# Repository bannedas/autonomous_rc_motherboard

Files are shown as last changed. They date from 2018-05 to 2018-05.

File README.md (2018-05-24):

# Autonomous RC motherboard

Remake of Benjamin Vedder made project https://github.com/vedderb/rise_sdvp

## Main

```
- Raspberry Compute module 3
	- HDMI
	- CAM0
	- ETHERNET
	- USB HOST (4 USB OUT)
	- microSD
- DAS board
- 2.4GHz radio by CC2520 
	- CC2592 extender
	- External antenna
- 420MHz - 470MHz radio by CC120
	- External antenna
-RTK-GNSS
	- UBLOX NEO M8P module
	- External antenna

- 40V to 12V 3A power
- 12V to 5V 1A power
- 12V to 3V3 2A power
- 3V3 to 1V8 500mA power

- 2x CAN output
- 4x PWM output
- 1 uart output

- Status LED for everything

```

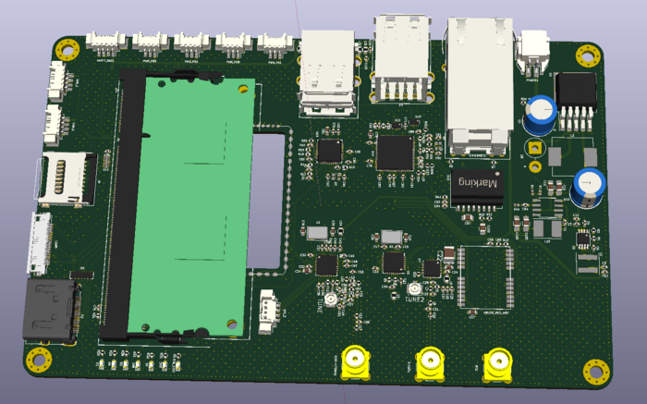
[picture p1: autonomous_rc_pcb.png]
PCB


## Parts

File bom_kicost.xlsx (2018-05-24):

Prj: | bom_kicost.xml |  |  |  | Board Qty: | 100
Co.: |  |  |  |  | Unit Cost: | $0.00
Prj date: | Thu 24 May 2018 02:57:31 PM CEST |  |  |  | Total Cost: | $0.00 |  |  |  | $0.00 | 0 |  |  |  | $0.00 | 0 |  |  |  | $0.00 | 0 |  |  |  | $0.00 | 0 |  |  |  | $0.00 | 0 |  |  |  | $0.00 | 0
$ date: | 2018-05-24 14:59:21
Global Part Info |  |  |  |  |  |  | Digi-Key |  |  |  |  | Farnell |  |  |  |  | Mouser |  |  |  |  | Newark |  |  |  |  | Rs Components |  |  |  |  | Tme
Refs | Value | Footprint | Manf# | Qty | Unit$ | Ext$ | Avail | Purch | Unit$ | Ext$ | Cat# | Avail | Purch | Unit$ | Ext$ | Cat# | Avail | Purch | Unit$ | Ext$ | Cat# | Avail | Purch | Unit$ | Ext$ | Cat# | Avail | Purch | Unit$ | Ext$ | Cat# | Avail | Purch | Unit$ | Ext$ | Cat#
A1 | RaspberryPiComputeModule | Don-Con:DDR2_TE_1473149-4 |  | 0 | $0.00 | $0.00
C1 | 10nF | Capacitors_SMD:C_0402 |  | 0 | $0.00 | $0.00
C10,C12 | 10uF | Capacitors_SMD:C_0805_HandSoldering |  | 0 | $0.00 | $0.00
C102 | 1n | Capacitors_SMD:C_0805 |  | 0 | $0.00 | $0.00
C105,C106 | 22uF | Capacitors_SMD:C_0805_HandSoldering |  | 0 | $0.00 | $0.00
C14 | 3.3nF | Capacitors_SMD:C_0402 |  | 0 | $0.00 | $0.00
C16,C19 | 15pF | Capacitors_SMD:C_0603 |  | 0 | $0.00 | $0.00
C2,C9,C11,C13 | 10uF | Capacitors_SMD:C_0402 |  | 0 | $0.00 | $0.00
C20,C23,C26 | 2.2uF | Capacitors_SMD:C_0402 |  | 0 | $0.00 | $0.00
C22 | 12uF | Capacitors_SMD:C_0402 |  | 0 | $0.00 | $0.00
C24,C25 | 1nF | Capacitors_SMD:C_0402 |  | 0 | $0.00 | $0.00
C27 | 12pF | Capacitors_SMD:C_0402 |  | 0 | $0.00 | $0.00
C28,C29,C53 | 2.2pF | Capacitors_SMD:C_0402 |  | 0 | $0.00 | $0.00
C3,C8 | 4.7uF | Capacitors_SMD:C_0402 |  | 0 | $0.00 | $0.00
C30 | 18pF | Capacitors_SMD:C_0402 |  | 0 | $0.00 | $0.00
C31 | 0.2pF | Capacitors_SMD:C_0402 |  | 0 | $0.00 | $0.00
C34,C57 | 2.2uF | Capacitors_SMD:C_0603 |  | 0 | $0.00 | $0.00
C35,C36 | 15p | Capacitors_SMD:C_0603 |  | 0 | $0.00 | $0.00
C4 | 1uF | Capacitors_SMD:C_0402 |  | 0 | $0.00 | $0.00
C45 | 1.8nF | Capacitors_SMD:C_0402 |  | 0 | $0.00 | $0.00
C48 | 39pF | Capacitors_SMD:C_0402 |  | 0 | $0.00 | $0.00
C5 | 100uF | Capacitor_THT:CP_Radial_D8.0mm_P3.50mm |  | 0 | $0.00 | $0.00
C50 | 56pF | Capacitors_SMD:C_0402 |  | 0 | $0.00 | $0.00
C52,C54,C55 | 5.1pF | Capacitors_SMD:C_0402 |  | 0 | $0.00 | $0.00
C56 | 6.2pF | Capacitors_SMD:C_0402 |  | 0 | $0.00 | $0.00
C6,C15,C17,C18,C21,C32,C33,C37-C44,C46,C47,C49,C51,C58 | 100nF | Capacitors_SMD:C_0402 |  | 0 | $0.00 | $0.00
C64,C67 | 9p | Capacitors_SMD:C_0402 | GRM1555C1H9R0CA01D | 0 | $0.00 | $0.00 | NonStk |  | $0.00 | $0.00 | 490-8232-1-ND (http://www.digikey.com/product-detail/en/murata-electronics-north-america/GRM1555C1H9R0CA01D/490-8232-1-ND/4380526) |  |  |  |  |  | NonStk |  | $0.00 | $0.00 | 81-GRM1555C1H9R0CA1D (https://www.mouser.com/ProductDetail/Murata-Electronics/GRM1555C1H9R0CA01D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)
C68 | 4u7 10V | Capacitors_SMD:C_0603 |  | 0 | $0.00 | $0.00
C7 | 1000uF | Capacitor_THT:CP_Radial_D8.0mm_P5.00mm | EEUFR1C102LB | 0 | $0.00 | $0.00 | 860 |  | $0.00 | $0.00 | P15332CT-ND (http://www.digikey.com/product-detail/en/panasonic-electronic-components/EEU-FR1C102LB/P15332CT-ND/3072212) |  |  |  |  |  | NonStk |  | $0.00 | $0.00 | 667-EEU-FR1C102LB (https://www.mouser.com/Search/Refine.aspx?Keyword=EEUFR1C102LB+) | 263 |  | $0.00 | $0.00 | 49W7393 (http://www.newark.com/webapp/wcs/stores/servlet/Search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) | 3800 |  |  |  | 708-3642 (http://it.rs-online.com/web/p/condensatori-elettrolitici/7083642P/)
C73 | 4u7 | Capacitors_SMD:C_0603 |  | 0 | $0.00 | $0.00
C74 | 1u | Capacitors_SMD:C_0402 |  | 0 | $0.00 | $0.00
C91,C92 | 6p | Capacitors_SMD:C_0402 |  | 0 | $0.00 | $0.00
C97 | 22n | Capacitors_SMD:C_0805 |  | 0 | $0.00 | $0.00
C98,C99,C103,C104 | 1n | Capacitors_SMD:C_0402 |  | 0 | $0.00 | $0.00
C59-C63,C65,C66,C69-C72,C76-C90,C93-C96,C100,C101 | 100n | Capacitors_SMD:C_0402 |  | 0 | $0.00 | $0.00
CAM0 | Conn_01x22 | MM-CONN:54548-2271 | 54548-2271 | 0 | $0.00 | $0.00 | 5312 |  | $0.00 | $0.00 | WM8828CT-ND (http://www.digikey.com/product-detail/en/molex-llc/0545482271/WM8828CT-ND/3197258) |  |  |  |  |  | 2773 |  | $0.00 | $0.00 | 538-54548-2271 (https://www.mouser.com/Search/Refine.aspx?Keyword=54548-2271+) | 24750 |  | $0.00 | $0.00 | 28W0905 (http://www.newark.com/molex/54548-2271/ffc-fpc-board-connector-zif-surface/dp/28W0905?st=54548-2271%20)
CAN_1,CAN_2,UART7_DAS1 | CONN_01X04 | Connectors_Molex:Molex_PicoBlade_53261-0471_04x1.25mm_Angled |  | 0 | $0.00 | $0.00
D1 | RTK_STAT | LEDs:LED_0603 |  | 0 | $0.00 | $0.00
D5,D6 | 3V3 | LEDs:LED_0603 |  | 0 | $0.00 | $0.00
D7 | 5V | LEDs:LED_0603 |  | 0 | $0.00 | $0.00
D8 | 1N5822 | PAUL-DIODE-SMD:D_DO-201AD_P5.08mm_Vertical_AnodeUp |  | 0 | $0.00 | $0.00
D2-D4 | LED | LEDs:LED_0603 |  | 0 | $0.00 | $0.00
ETHERNET1 | 08261L1T57-F | FS-Conn:0826-1L1T-57-F | 08261L1T57-F | 0 | $0.00 | $0.00 | 1929 |  | $0.00 | $0.00 | 507-1431-ND (http://www.digikey.com/scripts/DkSearch/dksus.dll?WT.z_header=search_go&lang=en) |  |  |  |  |  | 757 |  | $0.00 | $0.00 | 530-0826-1L1T-57-F (https://www.mouser.com/Search/Refine.aspx?Keyword=08261L1T57-F+)
J9 | Micro_SD_Card | Don-Con:microSD_Card_Receptacle_Wurth_693072010801 |  | 0 | $0.00 | $0.00
L1 | 4.7uH | Resistors_SMD:R_0805_HandSoldering | CPI0805E4R7R-10 | 0 | $0.00 | $0.00 | NonStk |  | $0.00 | $0.00 | CPI0805E4R7R-10-ND (http://www.digikey.com/scripts/DkSearch/dksus.dll?WT.z_header=search_go&lang=en) |  |  |  |  |  | 11435 |  | $0.00 | $0.00 | 875-CPI0805E4R7R-10 (https://www.mouser.com/Search/Refine.aspx?Keyword=CPI0805E4R7R-10+) | 1114 |  | $0.00 | $0.00 | 39Y3900 (http://www.newark.com/webapp/wcs/stores/servlet/Search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)
L11,L15 | 15n | Resistors_SMD:R_0402 |  | 0 | $0.00 | $0.00
L12,L13 | 27n | Resistors_SMD:R_0402 |  | 0 | $0.00 | $0.00
L16 | 43n | Resistors_SMD:R_0402 |  | 0 | $0.00 | $0.00
L17 | 22n | Resistors_SMD:R_0402 |  | 0 | $0.00 | $0.00
L18 | 56N | Resistors_SMD:R_0402 |  | 0 | $0.00 | $0.00
L19,L20 | BLM15PD121SN1D | Resistors_SMD:R_0402 |  | 0 | $0.00 | $0.00
L2 | 22uH | Inductors_SMD:L_Coilcraft_XAL5030 | VLCF5020T-220MR75-1 | 0 | $0.00 | $0.00 | 21355 |  | $0.00 | $0.00 | 445-3211-1-ND (http://www.digikey.com/product-detail/en/tdk-corporation/VLCF5020T-220MR75-1/445-3211-1-ND/1132852) |  |  |  |  |  | 6990 |  | $0.00 | $0.00 | 810-VLCF52T220MR751 (https://www.mouser.com/Search/Refine.aspx?Keyword=VLCF5020T-220MR75-1+) | NonStk |  | $0.00 | $0.00 | 91Y7126 (http://www.newark.com/tdk/vlcf5020t-220mr75-1/inductor-shielded-22uh-1a-20/dp/91Y7126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) | 280 |  | $0.00 | $0.00 | 614-2863 (http://it.rs-online.com/web/c/?searchTerm=VLCF5020T-220MR75-1+)
L29 | 4.7uH | Inductors_SMD:L_Taiyo-Yuden_NR-50xx_HandSoldering | SRN4018-4R7M | 0 | $0.00 | $0.00 | 38373 |  | $0.00 | $0.00 | SRN4018-4R7MCT-ND (http://www.digikey.com/product-detail/en/bourns-inc/SRN4018-4R7M/SRN4018-4R7MCT-ND/3821520) |  |  |  |  |  | 14094 |  | $0.00 | $0.00 | 652-SRN4018-4R7M (https://www.mouser.com/Search/Refine.aspx?Keyword=SRN4018-4R7M+) | 4833 |  | $0.00 | $0.00 | 54W0064 (http://www.newark.com/bourns/srn4018-4r7m/inductor-semi-shielded-4-7uh-1/dp/54W0064) | NonStk |  | $0.00 | $0.00 | 172-8355 (http://it.rs-online.com/web/p/induttori-avvolti-smd/1728355/)
L3 | 100uH | Inductors_SMD:L_Vishay_IHLP-4040 | MSS1210-104KED | 0 | $0.00 | $0.00 |  |  |  |  |  |  |  |  |  |  | 1939 |  | $0.00 | $0.00 | 994-MSS1210-104KED (https://www.mouser.com/ProductDetail/Coilcraft/MSS1210-104KED)
L4,L6,L14 | BEAD | Resistors_SMD:R_0603 | BLM18HE152SN1 | 0 | $0.00 | $0.00 | 94313 |  | $0.00 | $0.00 | 490-5216-1-ND (http://www.digikey.com/product-detail/en/murata-electronics-north-america/BLM18HE152SN1D/490-5216-1-ND/1948392) |  |  |  |  |  | NonStk |  |  |  | Not Assigned (https://www.mouser.com/ProductDetail/Murata-Electronics/BLM18HE152SN1) | 23044 |  | $0.00 | $0.00 | 87X8574 (http://www.newark.com/webapp/wcs/stores/servlet/Search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) | NonStk |  | $0.00 | $0.00 | 167-4980 (http://it.rs-online.com/web/p/ferriti/1674980/) | 22000 |  | $0.00 | $0.00 | BLM18HE152SN1D (https://www.tme.eu/en/details/blm18he152sn1d/ferrite-beads/murata/)
L5 | 4.7n | Resistors_SMD:R_0402 |  | 0 | $0.00 | $0.00
L7 | 1n | Resistors_SMD:R_0402 |  | 0 | $0.00 | $0.00
L8 | 2n | Resistors_SMD:R_0402 |  | 0 | $0.00 | $0.00
L9,L10 | 56n | Resistors_SMD:R_0402 |  | 0 | $0.00 | $0.00
L21-L28 | BLM18EG221SN1D | Resistors_SMD:R_0603 | BLM18EG221SN1D | 0 | $0.00 | $0.00 | 126995 |  | $0.00 | $0.00 | 490-3992-1-ND (http://www.digikey.com/product-detail/en/murata-electronics-north-america/BLM18EG221SN1D/490-3992-1-ND/1016252) |  |  |  |  |  |  |  |  |  |  | 6911 |  | $0.00 | $0.00 | 73M9090 (http://www.newark.com/webapp/wcs/stores/servlet/Search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) | 1375 |  | $0.00 | $0.00 | 724-1328 (http://it.rs-online.com/web/p/ferriti/7241328/) | NonStk |  | $0.00 | $0.00 | BLM18EG221SN1D (https://www.tme.eu/en/details/blm18eg221sn1d/ferrite-beads/murata/)
P1,P7 | USB_A_Vertical | Don-Con:USB_A_Stacked |  | 0 | $0.00 | $0.00
P2 | HDMI_PAUL | FS-Conn:HDMI_A_47151-1051 |  | 0 | $0.00 | $0.00
P3-P5 | SMA_SMD | Connectors:SMA_THT_Jack_Straight |  | 0 | $0.00 | $0.00
POWER1 | CONN_01X02 | Don-Con:DuraClik2 |  | 0 | $0.00 | $0.00
PWM_PA1,PWM_PB0,PWM_PB1,PWM_PB9 | CONN_01X03 | Connectors_Molex:Molex_PicoBlade_53261-0371_03x1.25mm_Angled |  | 0 | $0.00 | $0.00
R1 | 52.3k | Resistors_SMD:R_0402 |  | 0 | $0.00 | $0.00
R10 | 3.9K | Resistors_SMD:R_0402 |  | 0 | $0.00 | $0.00
R12 | 18R | Resistors_SMD:R_0402 |  | 0 | $0.00 | $0.00
R13 | 4.7R | Resistors_SMD:R_0402 |  | 0 | $0.00 | $0.00
R14,R16-R19 | 100k | Resistors_SMD:R_0402 |  | 0 | $0.00 | $0.00
R15 | 12k0 | Resistors_SMD:R_0402 |  | 0 | $0.00 | $0.00
R2,R33 | 10k | Resistors_SMD:R_0402 |  | 0 | $0.00 | $0.00
R20,R28,R29 | R | Resistors_SMD:R_0402 |  | 0 | $0.00 | $0.00
R22,R40 | 1M | Resistors_SMD:R_0402 |  | 0 | $0.00 | $0.00
R23 | 100K | Resistors_SMD:R_0402 |  | 0 | $0.00 | $0.00
R24 | DNP | Resistors_SMD:R_0402 |  | 0 | $0.00 | $0.00
R26 | 1k | Resistors_SMD:R_0402 |  | 0 | $0.00 | $0.00
R3 | 26.1k | Resistor_SMD:R_0402_1005Metric |  | 0 | $0.00 | $0.00
R34 | 12k4 | Resistors_SMD:R_0402 |  | 0 | $0.00 | $0.00
R35 | 12k | Resistors_SMD:R_0402 |  | 0 | $0.00 | $0.00
R4,R44 | 10k | Resistor_SMD:R_0402_1005Metric |  | 0 | $0.00 | $0.00
R41 | 10R | Resistors_SMD:R_0402 |  | 0 | $0.00 | $0.00
R42,R43 | 75R | Resistors_SMD:R_0402 |  | 0 | $0.00 | $0.00
R5,R25,R27,R30-R32 | 1K | Resistors_SMD:R_0402 |  | 0 | $0.00 | $0.00
R6,R7 | 120R | Resistors_SMD:R_0402 |  | 0 | $0.00 | $0.00
R8 | 10K | Resistors_SMD:R_0402 |  | 0 | $0.00 | $0.00
R9,R11 | 56K | Resistors_SMD:R_0402 |  | 0 | $0.00 | $0.00
R36-R39 | 49R9 | Resistors_SMD:R_0402 |  | 0 | $0.00 | $0.00
SPI_3 | CONN_01X04 | Connectors_Molex:Molex_PicoBlade_53398-0471_04x1.25mm_Straight |  | 0 | $0.00 | $0.00
U1 | MCP1603L | TO_SOT_Packages_SMD:TSOT-23-5 | MCP1603LT-180I/OS | 0 | $0.00 | $0.00 | NonStk |  | $0.00 | $0.00 | MCP1603LT-180I/OS-ND (http://www.digikey.com/scripts/DkSearch/dksus.dll?WT.z_header=search_go&lang=en) |  |  |  |  |  | NonStk |  | $0.00 | $0.00 | 579-MCP1603LT-180IOS (https://www.mouser.com/ProductDetail/Microchip-Technology/MCP1603LT-180I-OS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)
U10,U12 | ECMF04-4HSM10 | Housings_DFN_QFN:UDFN-10_1.35x2.6mm_Pitch0.5mm | ECMF04-4HSM10 | 0 | $0.00 | $0.00 | NonStk |  | $0.00 | $0.00 | 497-14242-2-ND (http://www.digikey.com/product-detail/en/stmicroelectronics/ECMF04-4HSM10/497-14242-2-ND/4552280) |  |  |  |  |  | 2949 |  | $0.00 | $0.00 | 511-ECMF04-4HSM10 (https://www.mouser.com/Search/Refine.aspx?Keyword=ECMF04-4HSM10+) | 3157 |  | $0.00 | $0.00 | 41Y1736 (http://www.newark.com/webapp/wcs/stores/servlet/Search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)
U11 | CM1624 | Don-Housing-DFN:UDFN-16-1EP_3.3x1.35mm_Pitch0.4mm | CM1624-08DE | 0 | $0.00 | $0.00 | NonStk |  | $0.00 | $0.00 | CM1624-08DEOSCT-ND (http://www.digikey.com/product-detail/en/on-semiconductor/CM1624-08DE/CM1624-08DEOSCT-ND/2442761) |  |  |  |  |  | NonStk |  | $0.00 | $0.00 | 748-CM1624-08DE (https://www.mouser.com/Search/Refine.aspx?Keyword=CM1624-08DE+) | NonStk |  | $0.00 | $0.00 | 55T2137 (http://www.newark.com/on-semiconductor/cm1624-08de/diode-emi-filter-esd-8ch-16-udfn/dp/55T2137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) | 50 |  | $0.00 | $0.00 | 800-9960 (http://it.rs-online.com/web/p/diodi-tvs/8009960/)
U13 | USB2514Bi | Don-Housing-QFN:QFN36_5m5X5m5 | USB2514B/M2 | 0 | $0.00 | $0.00 | 1776 |  | $0.00 | $0.00 | USB2514B/M2-ND (http://www.digikey.com/scripts/DkSearch/dksus.dll?WT.z_header=search_go&lang=en) |  |  |  |  |  | 4249 |  | $0.00 | $0.00 | 579-USB2514B/M2 (https://www.mouser.com/Search/Refine.aspx?Keyword=USB2514B%2FM2+) | 1421 |  | $0.00 | $0.00 | 31AC2618 (http://www.newark.com/webapp/wcs/stores/servlet/Search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) |  |  |  |  |  | NonStk |  | $0.00 | $0.00 | USB2514B/M2 (https://www.tme.eu/en/details/usb2514b_m2/usb-integrated-circuits/microchip-technology/)
U14 | LAN9514/LAN9514i | Housings_DFN_QFN:QFN-64-1EP_9x9mm_Pitch0.5mm | LAN9514-JZX | 0 | $0.00 | $0.00 | 2244 |  | $0.00 | $0.00 | 638-1087-ND (http://www.digikey.com/product-detail/en/microchip-technology/LAN9514-JZX/638-1087-ND/2166039) |  |  |  |  |  | 3560 |  | $0.00 | $0.00 | 886-LAN9514-JZX (https://www.mouser.com/ProductDetail/Microchip-Technology/LAN9514-JZX) | 34 |  | $0.00 | $0.00 | 69W9525 (http://www.newark.com/microchip/lan9514-jzx/usb-hub-ethernet-controller-100mbps/dp/69W9525?st=LAN9514-JZX%20) | 780 |  | $0.00 | $0.00 | 889-5130 (http://it.rs-online.com/web/p/controller-ethernet/8895130/)
U15 | Wurth_Magnetics_749010012A | FS-Magnetics:Wurth_749010012A | 749010012A | 0 | $0.00 | $0.00 |  |  |  |  |  |  |  |  |  |  |  |  |  |  |  | 428 |  | $0.00 | $0.00 | 55X3963 (http://www.newark.com/webapp/wcs/stores/servlet/Search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) | NonStk |  | $0.00 | $0.00 | 135-3807 (http://it.rs-online.com/web/p/trasformatori-per-reti-lan-ethernet/1353807/)
U16 | AP3512E | Package_SO:PowerIntegrations_SO-8 |  | 0 | $0.00 | $0.00
U2 | MCP16311/2 | Housings_SSOP:MSOP-8-1EP_3x3mm_Pitch0.65mm |  | 0 | $0.00 | $0.00
U3 | LM2576S-12/NOPB | Package_TO_SOT_SMD:TO-263-5_TabPin3 | LM2576S-12/NOPB | 0 | $0.00 | $0.00 | 2130 |  | $0.00 | $0.00 | LM2576S-12/NOPB-ND (http://www.digikey.com/scripts/DkSearch/dksus.dll?WT.z_header=search_go&lang=en) |  |  |  |  |  | 1401 |  | $0.00 | $0.00 | 926-LM2576S-12/NOPB (https://www.mouser.com/ProductDetail/Texas-Instruments/LM2576S-12-NOPB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) | 537 |  | $0.00 | $0.00 | 41K3687 (http://www.newark.com/webapp/wcs/stores/servlet/Search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) | 39 |  |  |  | 533-3197 (http://it.rs-online.com/web/p/convertitori-buck/5333197/) | 951 |  | $0.00 | $0.00 | LM2576S-12 (https://www.tme.eu/en/details/lm2576s-12/voltage-regulators-dcdc-circuits/texas-instruments/lm2576s-12nopb/)
U4 | Autopilot_module | Don-Mechanical:Autopilot |  | 0 | $0.00 | $0.00
U5 | ESD-8040 | FS-Diode:ESD8040 |  | 0 | $0.00 | $0.00
U6 | CC2520 | Housings_DFN_QFN:QFN-28-1EP_5x5mm_Pitch0.5mm | CC2520RHDR | 0 | $0.00 | $0.00 | 4009 |  | $0.00 | $0.00 | 296-22996-1-ND (http://www.digikey.com/product-detail/en/texas-instruments/CC2520RHDT/296-22996-1-ND/1770315) |  |  |  |  |  |  |  |  |  |  | 2900 |  | $0.00 | $0.00 | 33AC4955 (http://www.newark.com/webapp/wcs/stores/servlet/Search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)
U7 | CC2592 | Housings_DFN_QFN:QFN-16-1EP_4x4mm_Pitch0.65mm | CC2592RGVR | 0 | $0.00 | $0.00 | 7426 |  | $0.00 | $0.00 | 296-37475-1-ND (http://www.digikey.com/product-detail/en/texas-instruments/CC2592RGVR/296-37475-1-ND/4764659) |  |  |  |  |  | 4532 |  | $0.00 | $0.00 | 595-CC2592RGVR (https://www.mouser.com/ProductDetail/Texas-Instruments/CC2592RGVR) | 2787 |  | $0.00 | $0.00 | 33AC4958 (http://www.newark.com/webapp/wcs/stores/servlet/Search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)
U8 | CC112X | Housings_DFN_QFN:QFN-32-1EP_5x5mm_Pitch0.5mm |  | 0 | $0.00 | $0.00
U9 | UBLOX_NEO_M8P | PAUL-MODULE:U-BLOX-NEO-M8P |  | 0 | $0.00 | $0.00
X1 | 32Mhz | Crystals:Crystal_SMD_5032-4pin_5.0x3.2mm |  | 0 | $0.00 | $0.00
X2 | 32MHZ | Crystals:Crystal_SMD_5032-4pin_5.0x3.2mm |  | 0 | $0.00 | $0.00
X3 | XRCGB24M000F2P00R0 | Don-Timing:XRCGB |  | 0 | $0.00 | $0.00
X4 | XRCGB25M000F2P00R0 | Don-Timing:XRCGB |  | 0 | $0.00 | $0.00
Distributors scraped by KiCost® v.0.1.43 |  |  |  |  |  |  |  | 0 |  |  |  |  | 0 |  |  |  |  | 0 |  |  |  |  | 0 |  |  |  |  | 0 |  |  |  |  | 0
 |  |  |  |  |  |  |  | 0 | 0 | 0 |  |  | 0 | 0 | 0 |  |  | 0 | 0 | 0 |  |  | 0 | 0 | 0 |  |  | 0 | 0 | 0 |  |  | 0 | 0 | 0
 |  |  |  |  |  |  |  | 0 | 0 | 0 |  |  | 0 | 0 | 0 |  |  | 0 | 0 | 0 |  |  | 0 | 0 | 0 |  |  | 0 | 0 | 0 |  |  | 0 | 0 | 0
 |  |  |  |  |  |  |  | 0 | 0 | 0 |  |  | 0 | 0 | 0 |  |  | 0 | 0 | 0 |  |  | 0 | 0 | 0 |  |  | 0 | 0 | 0 |  |  | 0 | 0 | 0
 |  |  |  |  |  |  |  | 0 | 0 | 0 |  |  | 0 | 0 | 0 |  |  | 0 | 0 | 0 |  |  | 0 | 0 | 0 |  |  | 0 | 0 | 0 |  |  | 0 | 0 | 0
 |  |  |  |  |  |  |  | 0 | 0 | 0 |  |  | 0 | 0 | 0 |  |  | 0 | 0 | 0 |  |  | 0 | 0 | 0 |  |  | 0 | 0 | 0 |  |  | 0 | 0 | 0
 |  |  |  |  |  |  |  | 0 | 0 | 0 |  |  | 0 | 0 | 0 |  |  | 0 | 0 | 0 |  |  | 0 | 0 | 0 |  |  | 0 | 0 | 0 |  |  | 0 | 0 | 0
 |  |  |  |  |  |  |  | 0 | 0 | 0 |  |  | 0 | 0 | 0 |  |  | 0 | 0 | 0 |  |  | 0 | 0 | 0 |  |  | 0 | 0 | 0 |  |  | 0 | 0 | 0
 |  |  |  |  |  |  |  | 0 | 0 | 0 |  |  | 0 | 0 | 0 |  |  | 0 | 0 | 0 |  |  | 0 | 0 | 0 |  |  | 0 | 0 | 0 |  |  | 0 | 0 | 0
 |  |  |  |  |  |  |  | 0 | 0 | 0 |  |  | 0 | 0 | 0 |  |  | 0 | 0 | 0 |  |  | 0 | 0 | 0 |  |  | 0 | 0 | 0 |  |  | 0 | 0 | 0
 |  |  |  |  |  |  |  | 0 | 0 | 0 |  |  | 0 | 0 | 0 |  |  | 0 | 0 | 0 |  |  | 0 | 0 | 0 |  |  | 0 | 0 | 0 |  |  | 0 | 0 | 0
 |  |  |  |  |  |  |  | 0 | 0 | 0 |  |  | 0 | 0 | 0 |  |  | 0 | 0 | 0 |  |  | 0 | 0 | 0 |  |  | 0 | 0 | 0 |  |  | 0 | 0 | 0
 |  |  |  |  |  |  |  | 0 | 0 | 0 |  |  | 0 | 0 | 0 |  |  | 0 | 0 | 0 |  |  | 0 | 0 | 0 |  |  | 0 | 0 | 0 |  |  | 0 | 0 | 0
 |  |  |  |  |  |  |  | 0 | 0 | 0 |  |  | 0 | 0 | 0 |  |  | 0 | 0 | 0 |  |  | 0 | 0 | 0 |  |  | 0 | 0 | 0 |  |  | 0 | 0 | 0
 |  |  |  |  |  |  |  | 0 | 0 | 0 |  |  | 0 | 0 | 0 |  |  | 0 | 0 | 0 |  |  | 0 | 0 | 0 |  |  | 0 | 0 | 0 |  |  | 0 | 0 | 0
 |  |  |  |  |  |  |  | 0 | 0 | 0 |  |  | 0 | 0 | 0 |  |  | 0 | 0 | 0 |  |  | 0 | 0 | 0 |  |  | 0 | 0 | 0 |  |  | 0 | 0 | 0
 |  |  |  |  |  |  |  | 0 | 0 | 0 |  |  | 0 | 0 | 0 |  |  | 0 | 0 | 0 |  |  | 0 | 0 | 0 |  |  | 0 | 0 | 0 |  |  | 0 | 0 | 0
 |  |  |  |  |  |  |  | 0 | 0 | 0 |  |  | 0 | 0 | 0 |  |  | 0 | 0 | 0 |  |  | 0 | 0 | 0 |  |  | 0 | 0 | 0 |  |  | 0 | 0 | 0
 |  |  |  |  |  |  |  | 0 | 0 | 0 |  |  | 0 | 0 | 0 |  |  | 0 | 0 | 0 |  |  | 0 | 0 | 0 |  |  | 0 | 0 | 0 |  |  | 0 | 0 | 0
 |  |  |  |  |  |  |  | 0 | 0 | 0 |  |  | 0 | 0 | 0 |  |  | 0 | 0 | 0 |  |  | 0 | 0 | 0 |  |  | 0 | 0 | 0 |  |  | 0 | 0 | 0
 |  |  |  |  |  |  |  | 0 | 0 | 0 |  |  | 0 | 0 | 0 |  |  | 0 | 0 | 0 |  |  | 0 | 0 | 0 |  |  | 0 | 0 | 0 |  |  | 0 | 0 | 0
 |  |  |  |  |  |  |  | 0 | 0 | 0 |  |  | 0 | 0 | 0 |  |  | 0 | 0 | 0 |  |  | 0 | 0 | 0 |  |  | 0 | 0 | 0 |  |  | 0 | 0 | 0
 |  |  |  |  |  |  |  | 0 | 0 | 0 |  |  | 0 | 0 | 0 |  |  | 0 | 0 | 0 |  |  | 0 | 0 | 0 |  |  | 0 | 0 | 0 |  |  | 0 | 0 | 0
 |  |  |  |  |  |  |  | 0 | 0 | 0 |  |  | 0 | 0 | 0 |  |  | 0 | 0 | 0 |  |  | 0 | 0 | 0 |  |  | 0 | 0 | 0 |  |  | 0 | 0 | 0
 |  |  |  |  |  |  |  | 0 | 0 | 0 |  |  | 0 | 0 | 0 |  |  | 0 | 0 | 0 |  |  | 0 | 0 | 0 |  |  | 0 | 0 | 0 |  |  | 0 | 0 | 0
 |  |  |  |  |  |  |  | 0 | 0 | 0 |  |  | 0 | 0 | 0 |  |  | 0 | 0 | 0 |  |  | 0 | 0 | 0 |  |  | 0 | 0 | 0 |  |  | 0 | 0 | 0
 |  |  |  |  |  |  |  | 0 | 0 | 0 |  |  | 0 | 0 | 0 |  |  | 0 | 0 | 0 |  |  | 0 | 0 | 0 |  |  | 0 | 0 | 0 |  |  | 0 | 0 | 0
 |  |  |  |  |  |  |  | 0 | 0 | 0 |  |  | 0 | 0 | 0 |  |  | 0 | 0 | 0 |  |  | 0 | 0 | 0 |  |  | 0 | 0 | 0 |  |  | 0 | 0 | 0
 |  |  |  |  |  |  |  | 0 | 0 | 0 |  |  | 0 | 0 | 0 |  |  | 0 | 0 | 0 |  |  | 0 | 0 | 0 |  |  | 0 | 0 | 0 |  |  | 0 | 0 | 0
 |  |  |  |  |  |  |  | 0 | 0 | 0 |  |  | 0 | 0 | 0 |  |  | 0 | 0 | 0 |  |  | 0 | 0 | 0 |  |  | 0 | 0 | 0 |  |  | 0 | 0 | 0
 |  |  |  |  |  |  |  | 0 | 0 | 0 |  |  | 0 | 0 | 0 |  |  | 0 | 0 | 0 |  |  | 0 | 0 | 0 |  |  | 0 | 0 | 0 |  |  | 0 | 0 | 0
 |  |  |  |  |  |  |  | 0 | 0 | 0 |  |  | 0 | 0 | 0 |  |  | 0 | 0 | 0 |  |  | 0 | 0 | 0 |  |  | 0 | 0 | 0 |  |  | 0 | 0 | 0
 |  |  |  |  |  |  |  | 0 | 0 | 0 |  |  | 0 | 0 | 0 |  |  | 0 | 0 | 0 |  |  | 0 | 0 | 0 |  |  | 0 | 0 | 0 |  |  | 0 | 0 | 0
 |  |  |  |  |  |  |  | 0 | 0 | 0 |  |  | 0 | 0 | 0 |  |  | 0 | 0 | 0 |  |  | 0 | 0 | 0 |  |  | 0 | 0 | 0 |  |  | 0 | 0 | 0
 |  |  |  |  |  |  |  | 0 | 0 | 0 |  |  | 0 | 0 | 0 |  |  | 0 | 0 | 0 |  |  | 0 | 0 | 0 |  |  | 0 | 0 | 0 |  |  | 0 | 0 | 0
 |  |  |  |  |  |  |  | 0 | 0 | 0 |  |  | 0 | 0 | 0 |  |  | 0 | 0 | 0 |  |  | 0 | 0 | 0 |  |  | 0 | 0 | 0 |  |  | 0 | 0 | 0
 |  |  |  |  |  |  |  | 0 | 0 | 0 |  |  | 0 | 0 | 0 |  |  | 0 | 0 | 0 |  |  | 0 | 0 | 0 |  |  | 0 | 0 | 0 |  |  | 0 | 0 | 0
 |  |  |  |  |  |  |  | 0 | 0 | 0 |  |  | 0 | 0 | 0 |  |  | 0 | 0 | 0 |  |  | 0 | 0 | 0 |  |  | 0 | 0 | 0 |  |  | 0 | 0 | 0
 |  |  |  |  |  |  |  | 0 | 0 | 0 |  |  | 0 | 0 | 0 |  |  | 0 | 0 | 0 |  |  | 0 | 0 | 0 |  |  | 0 | 0 | 0 |  |  | 0 | 0 | 0
 |  |  |  |  |  |  |  | 0 | 0 | 0 |  |  | 0 | 0 | 0 |  |  | 0 | 0 | 0 |  |  | 0 | 0 | 0 |  |  | 0 | 0 | 0 |  |  | 0 | 0 | 0
 |  |  |  |  |  |  |  | 0 | 0 | 0 |  |  | 0 | 0 | 0 |  |  | 0 | 0 | 0 |  |  | 0 | 0 | 0 |  |  | 0 | 0 | 0 |  |  | 0 | 0 | 0
 |  |  |  |  |  |  |  | 0 | 0 | 0 |  |  | 0 | 0 | 0 |  |  | 0 | 0 | 0 |  |  | 0 | 0 | 0 |  |  | 0 | 0 | 0 |  |  | 0 | 0 | 0
 |  |  |  |  |  |  |  | 0 | 0 | 0 |  |  | 0 | 0 | 0 |  |  | 0 | 0 | 0 |  |  | 0 | 0 | 0 |  |  | 0 | 0 | 0 |  |  | 0 | 0 | 0
 |  |  |  |  |  |  |  | 0 | 0 | 0 |  |  | 0 | 0 | 0 |  |  | 0 | 0 | 0 |  |  | 0 | 0 | 0 |  |  | 0 | 0 | 0 |  |  | 0 | 0 | 0
 |  |  |  |  |  |  |  | 0 | 0 | 0 |  |  | 0 | 0 | 0 |  |  | 0 | 0 | 0 |  |  | 0 | 0 | 0 |  |  | 0 | 0 | 0 |  |  | 0 | 0 | 0
 |  |  |  |  |  |  |  | 0 | 0 | 0 |  |  | 0 | 0 | 0 |  |  | 0 | 0 | 0 |  |  | 0 | 0 | 0 |  |  | 0 | 0 | 0 |  |  | 0 | 0 | 0
 |  |  |  |  |  |  |  | 0 | 0 | 0 |  |  | 0 | 0 | 0 |  |  | 0 | 0 | 0 |  |  | 0 | 0 | 0 |  |  | 0 | 0 | 0 |  |  | 0 | 0 | 0
 |  |  |  |  |  |  |  | 0 | 0 | 0 |  |  | 0 | 0 | 0 |  |  | 0 | 0 | 0 |  |  | 0 | 0 | 0 |  |  | 0 | 0 | 0 |  |  | 0 | 0 | 0
 |  |  |  |  |  |  |  | 0 | 0 | 0 |  |  | 0 | 0 | 0 |  |  | 0 | 0 | 0 |  |  | 0 | 0 | 0 |  |  | 0 | 0 | 0 |  |  | 0 | 0 | 0
 |  |  |  |  |  |  |  | 0 | 0 | 0 |  |  | 0 | 0 | 0 |  |  | 0 | 0 | 0 |  |  | 0 | 0 | 0 |  |  | 0 | 0 | 0 |  |  | 0 | 0 | 0
 |  |  |  |  |  |  |  | 0 | 0 | 0 |  |  | 0 | 0 | 0 |  |  | 0 | 0 | 0 |  |  | 0 | 0 | 0 |  |  | 0 | 0 | 0 |  |  | 0 | 0 | 0
 |  |  |  |  |  |  |  | 0 | 0 | 0 |  |  | 0 | 0 | 0 |  |  | 0 | 0 | 0 |  |  | 0 | 0 | 0 |  |  | 0 | 0 | 0 |  |  | 0 | 0 | 0
 |  |  |  |  |  |  |  | 0 | 0 | 0 |  |  | 0 | 0 | 0 |  |  | 0 | 0 | 0 |  |  | 0 | 0 | 0 |  |  | 0 | 0 | 0 |  |  | 0 | 0 | 0
 |  |  |  |  |  |  |  | 0 | 0 | 0 |  |  | 0 | 0 | 0 |  |  | 0 | 0 | 0 |  |  | 0 | 0 | 0 |  |  | 0 | 0 | 0 |  |  | 0 | 0 | 0
 |  |  |  |  |  |  |  | 0 | 0 | 0 |  |  | 0 | 0 | 0 |  |  | 0 | 0 | 0 |  |  | 0 | 0 | 0 |  |  | 0 | 0 | 0 |  |  | 0 | 0 | 0
 |  |  |  |  |  |  |  | 0 | 0 | 0 |  |  | 0 | 0 | 0 |  |  | 0 | 0 | 0 |  |  | 0 | 0 | 0 |  |  | 0 | 0 | 0 |  |  | 0 | 0 | 0
 |  |  |  |  |  |  |  | 0 | 0 | 0 |  |  | 0 | 0 | 0 |  |  | 0 | 0 | 0 |  |  | 0 | 0 | 0 |  |  | 0 | 0 | 0 |  |  | 0 | 0 | 0
 |  |  |  |  |  |  |  | 0 | 0 | 0 |  |  | 0 | 0 | 0 |  |  | 0 | 0 | 0 |  |  | 0 | 0 | 0 |  |  | 0 | 0 | 0 |  |  | 0 | 0 | 0
 |  |  |  |  |  |  |  | 0 | 0 | 0 |  |  | 0 | 0 | 0 |  |  | 0 | 0 | 0 |  |  | 0 | 0 | 0 |  |  | 0 | 0 | 0 |  |  | 0 | 0 | 0
 |  |  |  |  |  |  |  | 0 | 0 | 0 |  |  | 0 | 0 | 0 |  |  | 0 | 0 | 0 |  |  | 0 | 0 | 0 |  |  | 0 | 0 | 0 |  |  | 0 | 0 | 0
 |  |  |  |  |  |  |  | 0 | 0 | 0 |  |  | 0 | 0 | 0 |  |  | 0 | 0 | 0 |  |  | 0 | 0 | 0 |  |  | 0 | 0 | 0 |  |  | 0 | 0 | 0
 |  |  |  |  |  |  |  | 0 | 0 | 0 |  |  | 0 | 0 | 0 |  |  | 0 | 0 | 0 |  |  | 0 | 0 | 0 |  |  | 0 | 0 | 0 |  |  | 0 | 0 | 0
 |  |  |  |  |  |  |  | 0 | 0 | 0 |  |  | 0 | 0 | 0 |  |  | 0 | 0 | 0 |  |  | 0 | 0 | 0 |  |  | 0 | 0 | 0 |  |  | 0 | 0 | 0
 |  |  |  |  |  |  |  | 0 | 0 | 0 |  |  | 0 | 0 | 0 |  |  | 0 | 0 | 0 |  |  | 0 | 0 | 0 |  |  | 0 | 0 | 0 |  |  | 0 | 0 | 0
 |  |  |  |  |  |  |  | 0 | 0 | 0 |  |  | 0 | 0 | 0 |  |  | 0 | 0 | 0 |  |  | 0 | 0 | 0 |  |  | 0 | 0 | 0 |  |  | 0 | 0 | 0
 |  |  |  |  |  |  |  | 0 | 0 | 0 |  |  | 0 | 0 | 0 |  |  | 0 | 0 | 0 |  |  | 0 | 0 | 0 |  |  | 0 | 0 | 0 |  |  | 0 | 0 | 0
 |  |  |  |  |  |  |  | 0 | 0 | 0 |  |  | 0 | 0 | 0 |  |  | 0 | 0 | 0 |  |  | 0 | 0 | 0 |  |  | 0 | 0 | 0 |  |  | 0 | 0 | 0
 |  |  |  |  |  |  |  | 0 | 0 | 0 |  |  | 0 | 0 | 0 |  |  | 0 | 0 | 0 |  |  | 0 | 0 | 0 |  |  | 0 | 0 | 0 |  |  | 0 | 0 | 0
 |  |  |  |  |  |  |  | 0 | 0 | 0 |  |  | 0 | 0 | 0 |  |  | 0 | 0 | 0 |  |  | 0 | 0 | 0 |  |  | 0 | 0 | 0 |  |  | 0 | 0 | 0
 |  |  |  |  |  |  |  | 0 | 0 | 0 |  |  | 0 | 0 | 0 |  |  | 0 | 0 | 0 |  |  | 0 | 0 | 0 |  |  | 0 | 0 | 0 |  |  | 0 | 0 | 0
 |  |  |  |  |  |  |  | 0 | 0 | 0 |  |  | 0 | 0 | 0 |  |  | 0 | 0 | 0 |  |  | 0 | 0 | 0 |  |  | 0 | 0 | 0 |  |  | 0 | 0 | 0
 |  |  |  |  |  |  |  | 0 | 0 | 0 |  |  | 0 | 0 | 0 |  |  | 0 | 0 | 0 |  |  | 0 | 0 | 0 |  |  | 0 | 0 | 0 |  |  | 0 | 0 | 0
 |  |  |  |  |  |  |  | 0 | 0 | 0 |  |  | 0 | 0 | 0 |  |  | 0 | 0 | 0 |  |  | 0 | 0 | 0 |  |  | 0 | 0 | 0 |  |  | 0 | 0 | 0
 |  |  |  |  |  |  |  | 0 | 0 | 0 |  |  | 0 | 0 | 0 |  |  | 0 | 0 | 0 |  |  | 0 | 0 | 0 |  |  | 0 | 0 | 0 |  |  | 0 | 0 | 0
 |  |  |  |  |  |  |  | 0 | 0 | 0 |  |  | 0 | 0 | 0 |  |  | 0 | 0 | 0 |  |  | 0 | 0 | 0 |  |  | 0 | 0 | 0 |  |  | 0 | 0 | 0
 |  |  |  |  |  |  |  | 0 | 0 | 0 |  |  | 0 | 0 | 0 |  |  | 0 | 0 | 0 |  |  | 0 | 0 | 0 |  |  | 0 | 0 | 0 |  |  | 0 | 0 | 0
 |  |  |  |  |  |  |  | 0 | 0 | 0 |  |  | 0 | 0 | 0 |  |  | 0 | 0 | 0 |  |  | 0 | 0 | 0 |  |  | 0 | 0 | 0 |  |  | 0 | 0 | 0
 |  |  |  |  |  |  |  | 0 | 0 | 0 |  |  | 0 | 0 | 0 |  |  | 0 | 0 | 0 |  |  | 0 | 0 | 0 |  |  | 0 | 0 | 0 |  |  | 0 | 0 | 0
 |  |  |  |  |  |  |  | 0 | 0 | 0 |  |  | 0 | 0 | 0 |  |  | 0 | 0 | 0 |  |  | 0 | 0 | 0 |  |  | 0 | 0 | 0 |  |  | 0 | 0 | 0
 |  |  |  |  |  |  |  | 0 | 0 | 0 |  |  | 0 | 0 | 0 |  |  | 0 | 0 | 0 |  |  | 0 | 0 | 0 |  |  | 0 | 0 | 0 |  |  | 0 | 0 | 0
 |  |  |  |  |  |  |  | 0 | 0 | 0 |  |  | 0 | 0 | 0 |  |  | 0 | 0 | 0 |  |  | 0 | 0 | 0 |  |  | 0 | 0 | 0 |  |  | 0 | 0 | 0
 |  |  |  |  |  |  |  | 0 | 0 | 0 |  |  | 0 | 0 | 0 |  |  | 0 | 0 | 0 |  |  | 0 | 0 | 0 |  |  | 0 | 0 | 0 |  |  | 0 | 0 | 0
 |  |  |  |  |  |  |  | 0 | 0 | 0 |  |  | 0 | 0 | 0 |  |  | 0 | 0 | 0 |  |  | 0 | 0 | 0 |  |  | 0 | 0 | 0 |  |  | 0 | 0 | 0
 |  |  |  |  |  |  |  | 0 | 0 | 0 |  |  | 0 | 0 | 0 |  |  | 0 | 0 | 0 |  |  | 0 | 0 | 0 |  |  | 0 | 0 | 0 |  |  | 0 | 0 | 0
 |  |  |  |  |  |  |  | 0 | 0 | 0 |  |  | 0 | 0 | 0 |  |  | 0 | 0 | 0 |  |  | 0 | 0 | 0 |  |  | 0 | 0 | 0 |  |  | 0 | 0 | 0
 |  |  |  |  |  |  |  | 0 | 0 | 0 |  |  | 0 | 0 | 0 |  |  | 0 | 0 | 0 |  |  | 0 | 0 | 0 |  |  | 0 | 0 | 0 |  |  | 0 | 0 | 0
 |  |  |  |  |  |  |  | 0 | 0 | 0 |  |  | 0 | 0 | 0 |  |  | 0 | 0 | 0 |  |  | 0 | 0 | 0 |  |  | 0 | 0 | 0 |  |  | 0 | 0 | 0
 |  |  |  |  |  |  |  | 0 | 0 | 0 |  |  | 0 | 0 | 0 |  |  | 0 | 0 | 0 |  |  | 0 | 0 | 0 |  |  | 0 | 0 | 0 |  |  | 0 | 0 | 0
 |  |  |  |  |  |  |  | 0 | 0 | 0 |  |  | 0 | 0 | 0 |  |  | 0 | 0 | 0 |  |  | 0 | 0 | 0 |  |  | 0 | 0 | 0 |  |  | 0 | 0 | 0
 |  |  |  |  |  |  |  | 0 | 0 | 0 |  |  | 0 | 0 | 0 |  |  | 0 | 0 | 0 |  |  | 0 | 0 | 0 |  |  | 0 | 0 | 0 |  |  | 0 | 0 | 0
 |  |  |  |  |  |  |  | 0 | 0 | 0 |  |  | 0 | 0 | 0 |  |  | 0 | 0 | 0 |  |  | 0 | 0 | 0 |  |  | 0 | 0 | 0 |  |  | 0 | 0 | 0
 |  |  |  |  |  |  |  | 0 | 0 | 0 |  |  | 0 | 0 | 0 |  |  | 0 | 0 | 0 |  |  | 0 | 0 | 0 |  |  | 0 | 0 | 0 |  |  | 0 | 0 | 0
 |  |  |  |  |  |  |  | 0 | 0 | 0 |  |  | 0 | 0 | 0 |  |  | 0 | 0 | 0 |  |  | 0 | 0 | 0 |  |  | 0 | 0 | 0 |  |  | 0 | 0 | 0
 |  |  |  |  |  |  |  | 0 | 0 | 0 |  |  | 0 | 0 | 0 |  |  | 0 | 0 | 0 |  |  | 0 | 0 | 0 |  |  | 0 | 0 | 0 |  |  | 0 | 0 | 0
 |  |  |  |  |  |  |  | 0 | 0 | 0 |  |  | 0 | 0 | 0 |  |  | 0 | 0 | 0 |  |  | 0 | 0 | 0 |  |  | 0 | 0 | 0 |  |  | 0 | 0 | 0
 |  |  |  |  |  |  |  | 0 | 0 | 0 |  |  | 0 | 0 | 0 |  |  | 0 | 0 | 0 |  |  | 0 | 0 | 0 |  |  | 0 | 0 | 0 |  |  | 0 | 0 | 0
 |  |  |  |  |  |  |  | 0 | 0 | 0 |  |  | 0 | 0 | 0 |  |  | 0 | 0 | 0 |  |  | 0 | 0 | 0 |  |  | 0 | 0 | 0 |  |  | 0 | 0 | 0
 |  |  |  |  |  |  |  | 0 | 0 | 0 |  |  | 0 | 0 | 0 |  |  | 0 | 0 | 0 |  |  | 0 | 0 | 0 |  |  | 0 | 0 | 0 |  |  | 0 | 0 | 0
 |  |  |  |  |  |  |  | 0 | 0 | 0 |  |  | 0 | 0 | 0 |  |  | 0 | 0 | 0 |  |  | 0 | 0 | 0 |  |  | 0 | 0 | 0 |  |  | 0 | 0 | 0
 |  |  |  |  |  |  |  | 0 | 0 | 0 |  |  | 0 | 0 | 0 |  |  | 0 | 0 | 0 |  |  | 0 | 0 | 0 |  |  | 0 | 0 | 0 |  |  | 0 | 0 | 0
 |  |  |  |  |  |  |  | 0 | 0 | 0 |  |  | 0 | 0 | 0 |  |  | 0 | 0 | 0 |  |  | 0 | 0 | 0 |  |  | 0 | 0 | 0 |  |  | 0 | 0 | 0
 |  |  |  |  |  |  |  | 0 | 0 | 0 |  |  | 0 | 0 | 0 |  |  | 0 | 0 | 0 |  |  | 0 | 0 | 0 |  |  | 0 | 0 | 0 |  |  | 0 | 0 | 0
 |  |  |  |  |  |  |  | 0 | 0 | 0 |  |  | 0 | 0 | 0 |  |  | 0 | 0 | 0 |  |  | 0 | 0 | 0 |  |  | 0 | 0 | 0 |  |  | 0 | 0 | 0
 |  |  |  |  |  |  |  | 0 | 0 | 0 |  |  | 0 | 0 | 0 |  |  | 0 | 0 | 0 |  |  | 0 | 0 | 0 |  |  | 0 | 0 | 0 |  |  | 0 | 0 | 0
 |  |  |  |  |  |  |  | 0 | 0 | 0 |  |  | 0 | 0 | 0 |  |  | 0 | 0 | 0 |  |  | 0 | 0 | 0 |  |  | 0 | 0 | 0 |  |  | 0 | 0 | 0
 |  |  |  |  |  |  |  | 0 | 0 | 0 |  |  | 0 | 0 | 0 |  |  | 0 | 0 | 0 |  |  | 0 | 0 | 0 |  |  | 0 | 0 | 0 |  |  | 0 | 0 | 0
 |  |  |  |  |  |  |  | 0 | 0 | 0 |  |  | 0 | 0 | 0 |  |  | 0 | 0 | 0 |  |  | 0 | 0 | 0 |  |  | 0 | 0 | 0 |  |  | 0 | 0 | 0
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

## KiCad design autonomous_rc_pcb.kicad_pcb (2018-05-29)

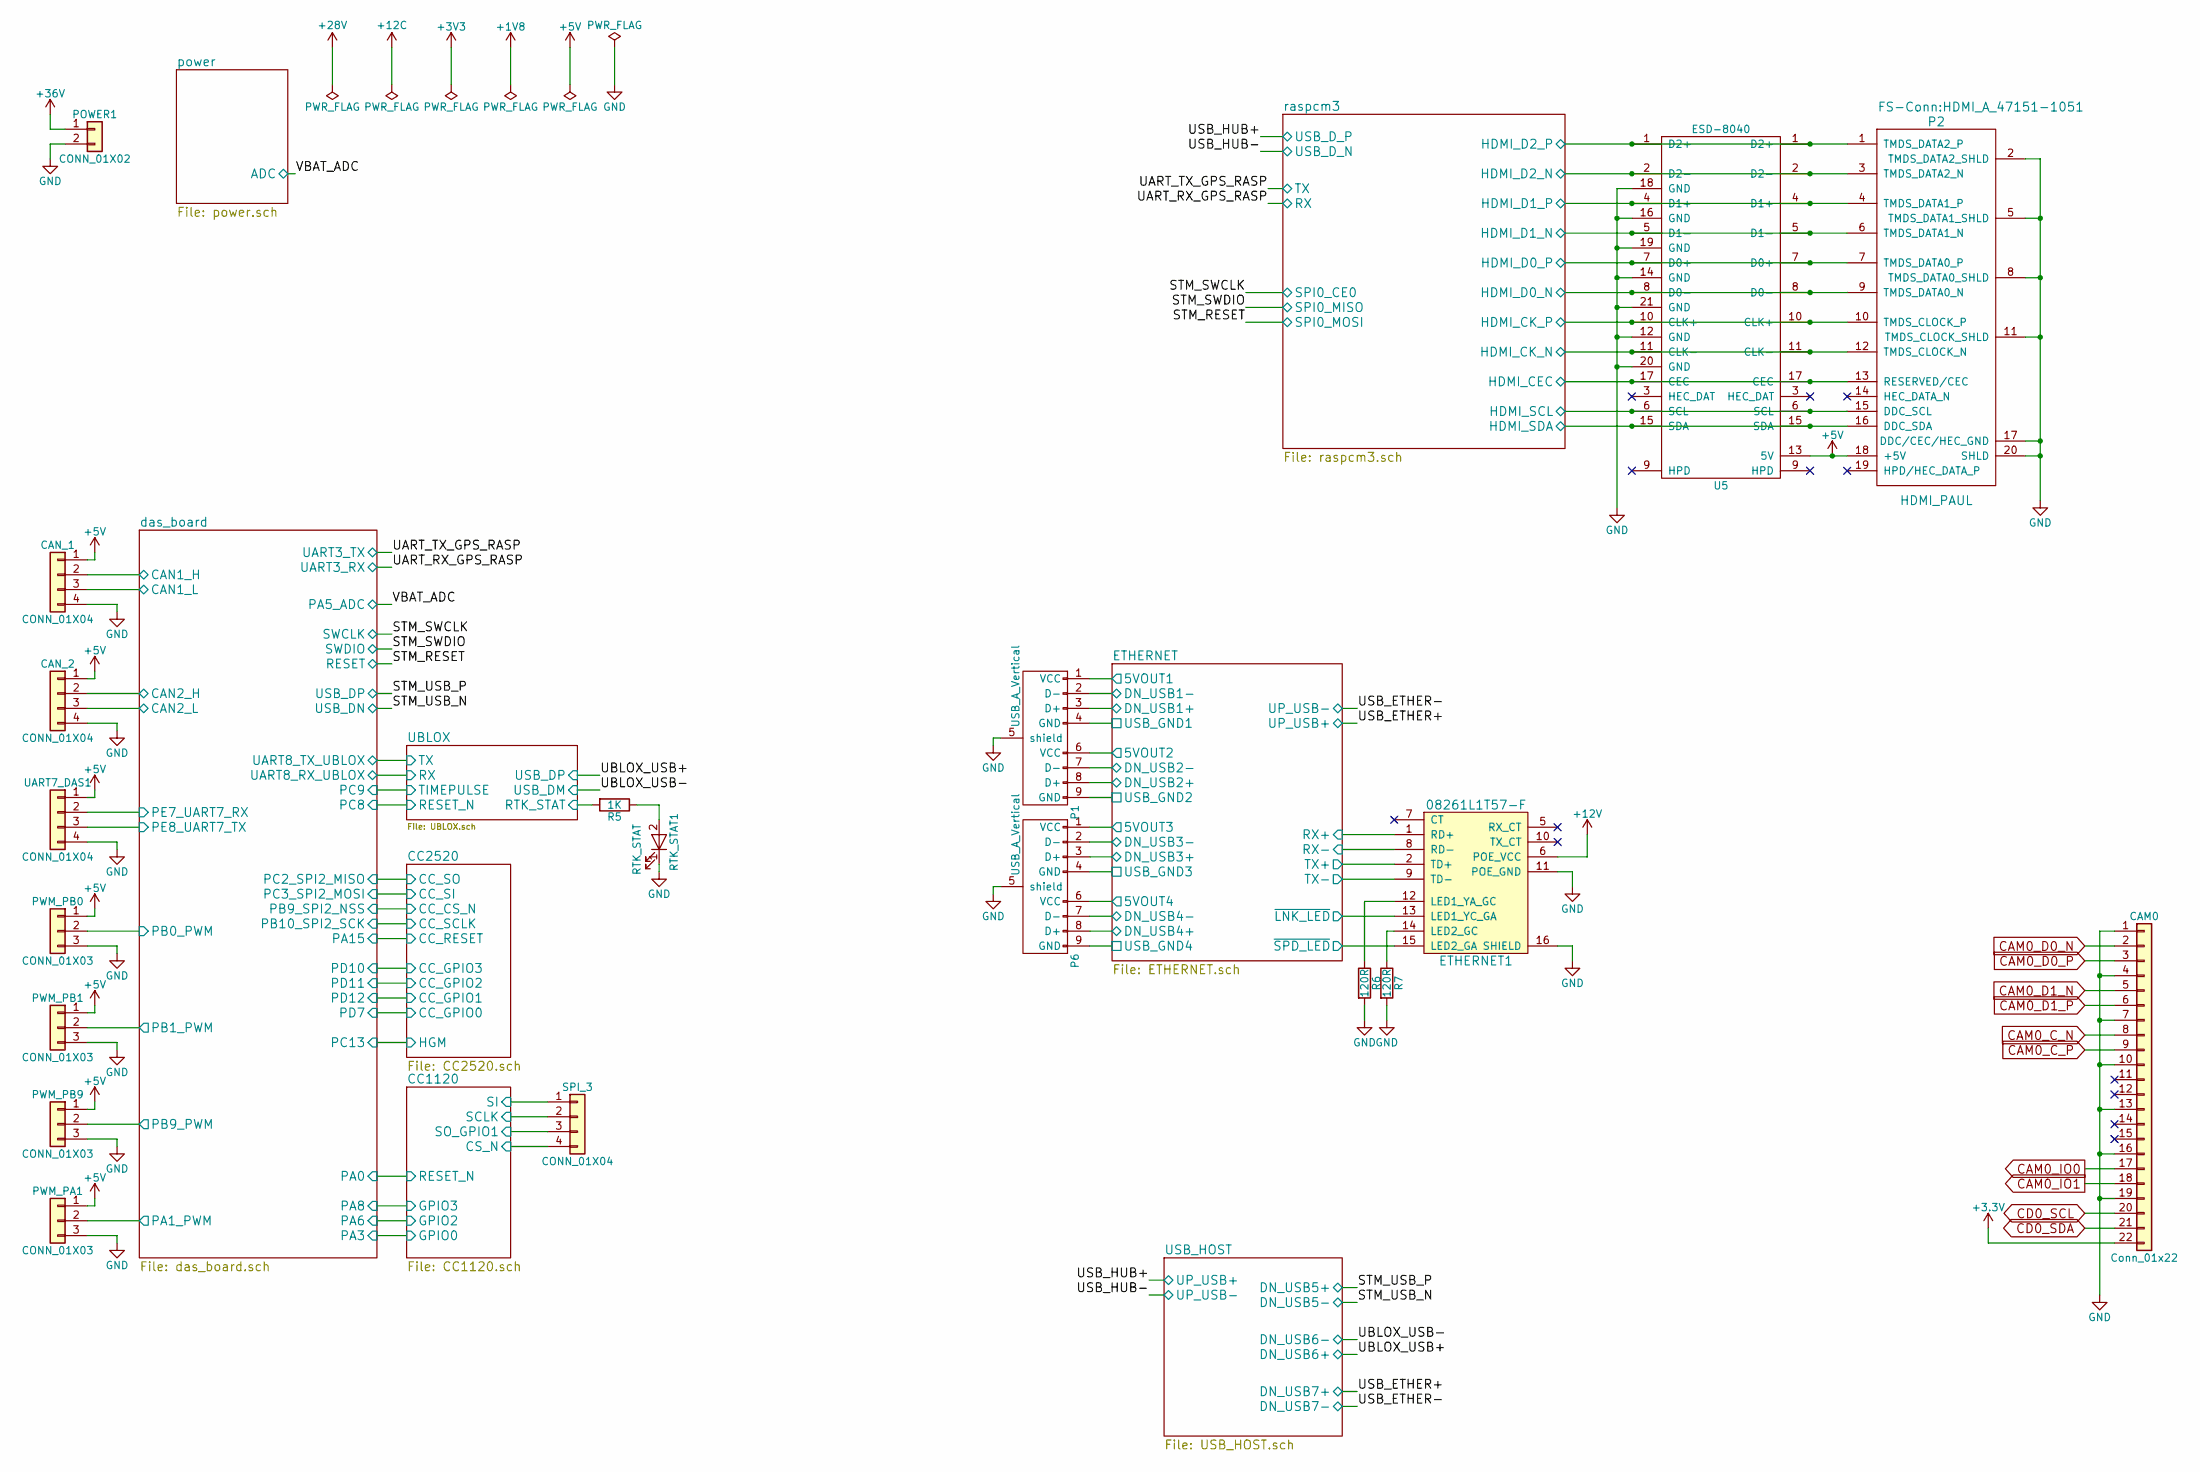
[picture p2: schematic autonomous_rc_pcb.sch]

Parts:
CAM0: Conn_01x22; 54548-2271; MPN 54548-2271
CAN_1, CAN_2: CONN_01X04; Molex_PicoBlade_53261-0471_04x1.25mm_Angled
ETHERNET1: 08261L1T57-F; 0826-1L1T-57-F; MPN 08261L1T57-F
P1, P6: USB_A_Vertical; USB-A-vertical
P2: HDMI_PAUL; HDMI_A_47151-1051
POWER1: CONN_01X02; DuraClik2
PWM_PA1: CONN_01X03; Molex_PicoBlade_53261-0371_03x1.25mm_Angled
PWM_PB0, PWM_PB1, PWM_PB9: CONN_01X03; Molex_PicoBlade_53261-0371_03x1.25mm_Angled
R5: 1K; R_0402
R6, R7: 120R; R_0402
RTK_STAT1: RTK_STAT; LED_0603
SPI_3: CONN_01X04; Molex_PicoBlade_53398-0471_04x1.25mm_Straight
U5: ESD-8040; ESD8040
UART7_DAS1: CONN_01X04; Molex_PicoBlade_53261-0471_04x1.25mm_Angled

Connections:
+5V: CAN_1.1, CAN_2.1, P2.18 (+5V), PWM_PA1.1, PWM_PB0.1, PWM_PB1.1, PWM_PB9.1, U5.13 (5V), UART7_DAS1.1; also elsewhere on the board
+12V: ETHERNET1.6 (POE_VCC); also elsewhere on the board
+36V: POWER1.1; also elsewhere on the board
/CC1120/CS_N: SPI_3.4; also elsewhere on the board
/CC1120/SCLK: SPI_3.2; also elsewhere on the board
/CC1120/SI: SPI_3.1; also elsewhere on the board
/CC1120/SO_GPIO1: SPI_3.3; also elsewhere on the board
/ETHERNET/5VOUT3: P1.1 (VCC); also elsewhere on the board
/ETHERNET/5VOUT4: P1.6 (VCC); also elsewhere on the board
/ETHERNET/DN_USB3+: P1.3 (D+); also elsewhere on the board
/ETHERNET/DN_USB3-: P1.2 (D-); also elsewhere on the board
/ETHERNET/DN_USB4+: P1.8 (D+); also elsewhere on the board
/ETHERNET/DN_USB4-: P1.7 (D-); also elsewhere on the board
/ETHERNET/RX+: ETHERNET1.1 (RD+); also elsewhere on the board
/ETHERNET/RX-: ETHERNET1.8 (RD-); also elsewhere on the board
/ETHERNET/TX+: ETHERNET1.2 (TD+); also elsewhere on the board
/ETHERNET/TX-: ETHERNET1.9 (TD-); also elsewhere on the board
/ETHERNET/USB_GND3: P1.4 (GND); also elsewhere on the board
/ETHERNET/USB_GND4: P1.9 (GND); also elsewhere on the board
/ETHERNET/~LNK_LED: ETHERNET1.13 (LED1_YC_GA); also elsewhere on the board
/ETHERNET/~SPD_LED: ETHERNET1.15 (LED2_GA); also elsewhere on the board
/UBLOX/RTK_STAT: R5.2; also elsewhere on the board
/das_board/CAN1_H: CAN_1.2; also elsewhere on the board
/das_board/CAN1_L: CAN_1.3; also elsewhere on the board
/das_board/CAN2_H: CAN_2.2; also elsewhere on the board
/das_board/CAN2_L: CAN_2.3; also elsewhere on the board
/das_board/PA1_PWM: PWM_PA1.2; also elsewhere on the board
/das_board/PB0_PWM: PWM_PB0.2; also elsewhere on the board
/das_board/PB1_PWM: PWM_PB1.2; also elsewhere on the board
/das_board/PB9_PWM: PWM_PB9.2; also elsewhere on the board
/das_board/PE7_UART7_RX: UART7_DAS1.2; also elsewhere on the board
/das_board/PE8_UART7_TX: UART7_DAS1.3; also elsewhere on the board
/raspcm3/HDMI_CEC: P2.13 (RESERVED/CEC), U5.17 (CEC); also elsewhere on the board
/raspcm3/HDMI_CK_N: P2.12 (TMDS_CLOCK_N), U5.11 (CLK-); also elsewhere on the board
/raspcm3/HDMI_CK_P: P2.10 (TMDS_CLOCK_P), U5.10 (CLK+); also elsewhere on the board
/raspcm3/HDMI_D0_N: P2.9 (TMDS_DATA0_N), U5.8 (D0-); also elsewhere on the board
/raspcm3/HDMI_D0_P: P2.7 (TMDS_DATA0_P), U5.7 (D0+); also elsewhere on the board
/raspcm3/HDMI_D1_N: P2.6 (TMDS_DATA1_N), U5.5 (D1-); also elsewhere on the board
/raspcm3/HDMI_D1_P: P2.4 (TMDS_DATA1_P), U5.4 (D1+); also elsewhere on the board
/raspcm3/HDMI_D2_N: P2.3 (TMDS_DATA2_N), U5.2 (D2-); also elsewhere on the board
/raspcm3/HDMI_D2_P: P2.1 (TMDS_DATA2_P), U5.1 (D2+); also elsewhere on the board
/raspcm3/HDMI_SCL: P2.15 (DDC_SCL), U5.6 (SCL); also elsewhere on the board
/raspcm3/HDMI_SDA: P2.16 (DDC_SDA), U5.15 (SDA); also elsewhere on the board
CAM0_C_N: CAM0.8; also elsewhere on the board
CAM0_C_P: CAM0.9; also elsewhere on the board
CAM0_D0_N: CAM0.2; also elsewhere on the board
CAM0_D0_P: CAM0.3; also elsewhere on the board
CAM0_D1_N: CAM0.5; also elsewhere on the board
CAM0_D1_P: CAM0.6; also elsewhere on the board
CAM0_IO0: CAM0.17; also elsewhere on the board
CAM0_IO1: CAM0.18; also elsewhere on the board
CD0_SCL: CAM0.20; also elsewhere on the board
CD0_SDA: CAM0.21; also elsewhere on the board
GND: CAM0.1, CAM0.4, CAM0.7, CAM0.10, CAM0.13, CAM0.16, CAM0.19, CAN_1.4, CAN_2.4, ETHERNET1.11 (POE_GND), ETHERNET1.16 (SHIELD), P1.5 (shield), P2.2 (TMDS_DATA2_SHLD), P2.5 (TMDS_DATA1_SHLD), P2.8 (TMDS_DATA0_SHLD), P2.11 (TMDS_CLOCK_SHLD), P2.17 (DDC/CEC/HEC_GND), P2.20 (SHLD), P6.5 (shield), POWER1.2, PWM_PA1.3, PWM_PB0.3, PWM_PB1.3, PWM_PB9.3, R6.2, R7.2, RTK_STAT1.1 (K), U5.12 (GND), U5.14 (GND), U5.16 (GND), U5.18 (GND), U5.19 (GND), U5.20 (GND), U5.21 (GND), UART7_DAS1.4; also elsewhere on the board
unnamed 253: R5.1, RTK_STAT1.2 (A); also elsewhere on the board
unnamed: ETHERNET1.12 (LED1_YA_GC), R6.1
unnamed: ETHERNET1.14 (LED2_GC), R7.1

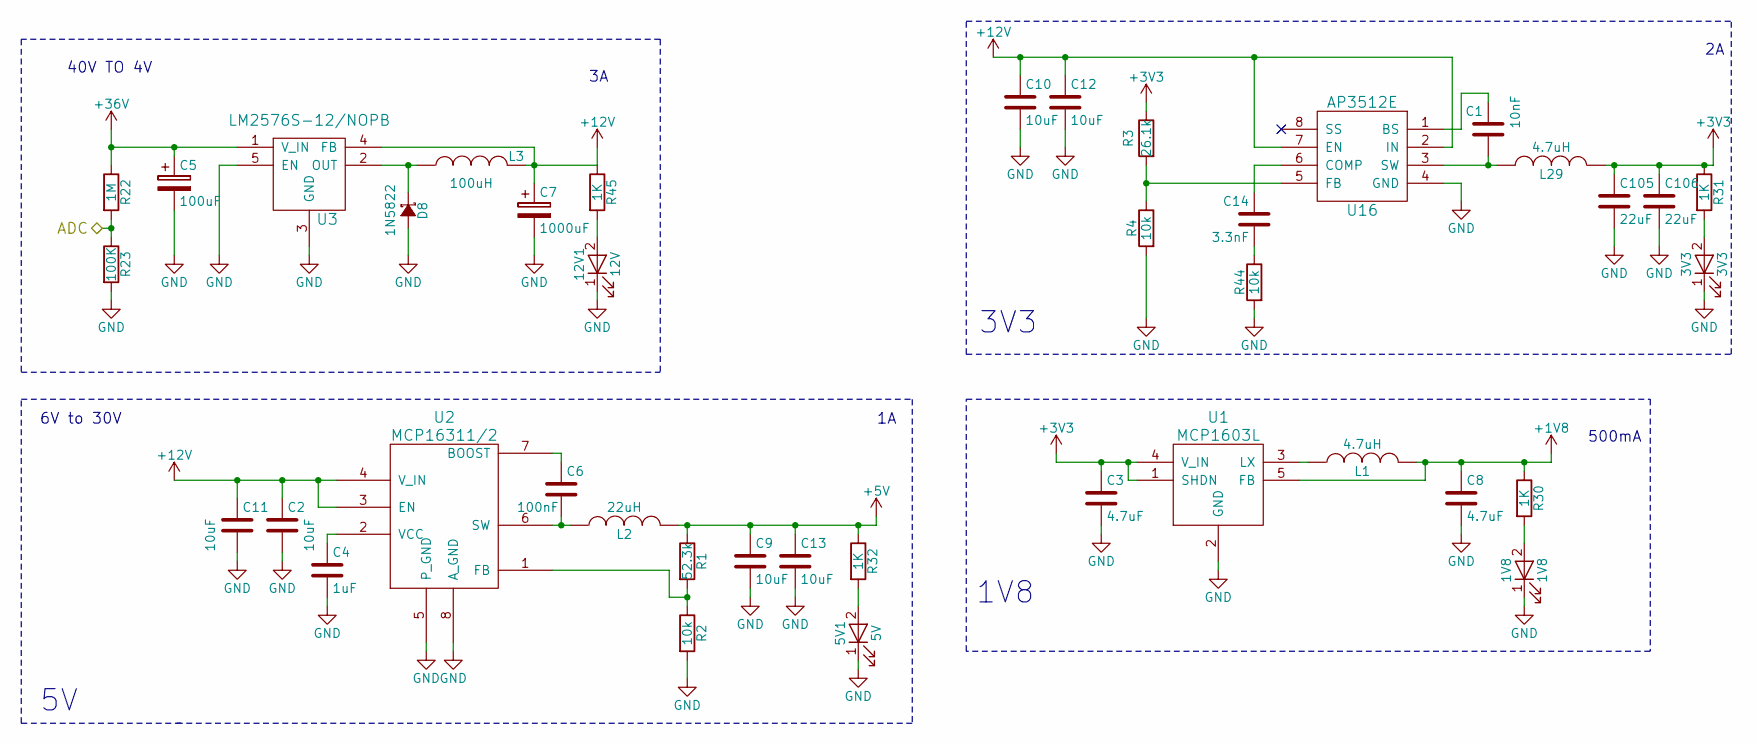
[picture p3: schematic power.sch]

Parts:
1V8: 1V8; LED_0603
3V3: 3V3; LED_0603
5V1: 5V; LED_0603
12V1: 12V; LED_0603
C1: 10nF; C_0402
C2, C9, C11, C13: 10uF; C_0402
C3, C8: 4.7uF; C_0402
C4: 1uF; C_0402
C5: 100uF; CP_Radial_D8.0mm_P3.50mm
C6: 100nF; C_0402
C7: 1000uF; CP_Radial_D8.0mm_P5.00mm; MPN EEUFR1C102LB
C10, C12: 10uF; C_0805_HandSoldering
C14: 3.3nF; C_0402
C105, C106: 22uF; C_0805_HandSoldering
D8: 1N5822; D_DO-201AD_P5.08mm_Vertical_AnodeUp
L1: 4.7uH; R_0805_HandSoldering; MPN CPI0805E4R7R-10
L2: 22uH; L_Coilcraft_XAL5030; MPN VLCF5020T-220MR75-1
L3: 100uH; L_Vishay_IHLP-4040; MPN MSS1210-104KED
L29: 4.7uH; L_Taiyo-Yuden_NR-50xx_HandSoldering; MPN SRN4018-4R7M
R1: 52.3k; R_0402
R2: 10k; R_0402
R3: 26.1k; R_0402_1005Metric
R4, R44: 10k; R_0402_1005Metric
R22: 1M; R_0402
R23: 100K; R_0402
R30, R31, R32, R45: 1K; R_0402
U1: MCP1603L; TSOT-23-5; MPN MCP1603LT-180I/OS
U2: MCP16311/2; MSOP-8-1EP_3x3mm_Pitch0.65mm
U3: LM2576S-12/NOPB; TO-263-5_TabPin3; MPN LM2576S-12/NOPB
U16: AP3512E; PowerIntegrations_SO-8

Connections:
+1V8: C8.1, L1.2, R30.1, U1.5 (FB); also elsewhere on the board
+5V: C9.1, C13.1, L2.2, R1.1, R32.1; also elsewhere on the board
+12V: C2.1, C7.1, C10.1, C11.1, C12.1, L3.2, R45.1, U2.3 (EN), U2.4 (V_IN), U3.4 (FB), U16.2 (IN), U16.7 (EN); also elsewhere on the board
+36V: C5.1, R22.1, U3.1 (V_IN); also elsewhere on the board
/VBAT_ADC: R22.2, R23.1; also elsewhere on the board
GND: 1V8.1 (K), 3V3.1 (K), 5V1.1 (K), 12V1.1 (K), C2.2, C3.2, C4.2, C5.2, C7.2, C8.2, C9.2, C10.2, C11.2, C12.2, C13.2, C105.2, C106.2, D8.A, R2.2, R4.2, R23.2, R44.2, U1.2 (GND), U2.5 (P_GND), U2.8 (A_GND), U3.3 (GND), U3.5 (EN), U16.4 (GND); also elsewhere on the board
unnamed: 12V1.2 (A), R45.2
unnamed: C1.1, U16.1 (BS)
unnamed: C1.2, L29.2, U16.3 (SW)
unnamed: C4.1, U2.2 (VCC)
unnamed: C6.1, U2.7 (BOOST)
unnamed: C6.2, L2.1, U2.6 (SW)
unnamed: C14.1, U16.6 (COMP)
unnamed: C14.2, R44.1
unnamed: 1V8.2 (A), R30.2
unnamed: 3V3.2 (A), R31.2
unnamed 259: 5V1.2 (A), R32.2; also elsewhere on the board
unnamed: D8.K, L3.1, U3.2 (OUT)
unnamed: L1.1, U1.3 (LX)
unnamed: R1.2, R2.1, U2.1 (FB)
unnamed: R3.2, R4.1, U16.5 (FB)

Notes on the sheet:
6V to 30V
1V8
3V3
500mA
40V TO 4V

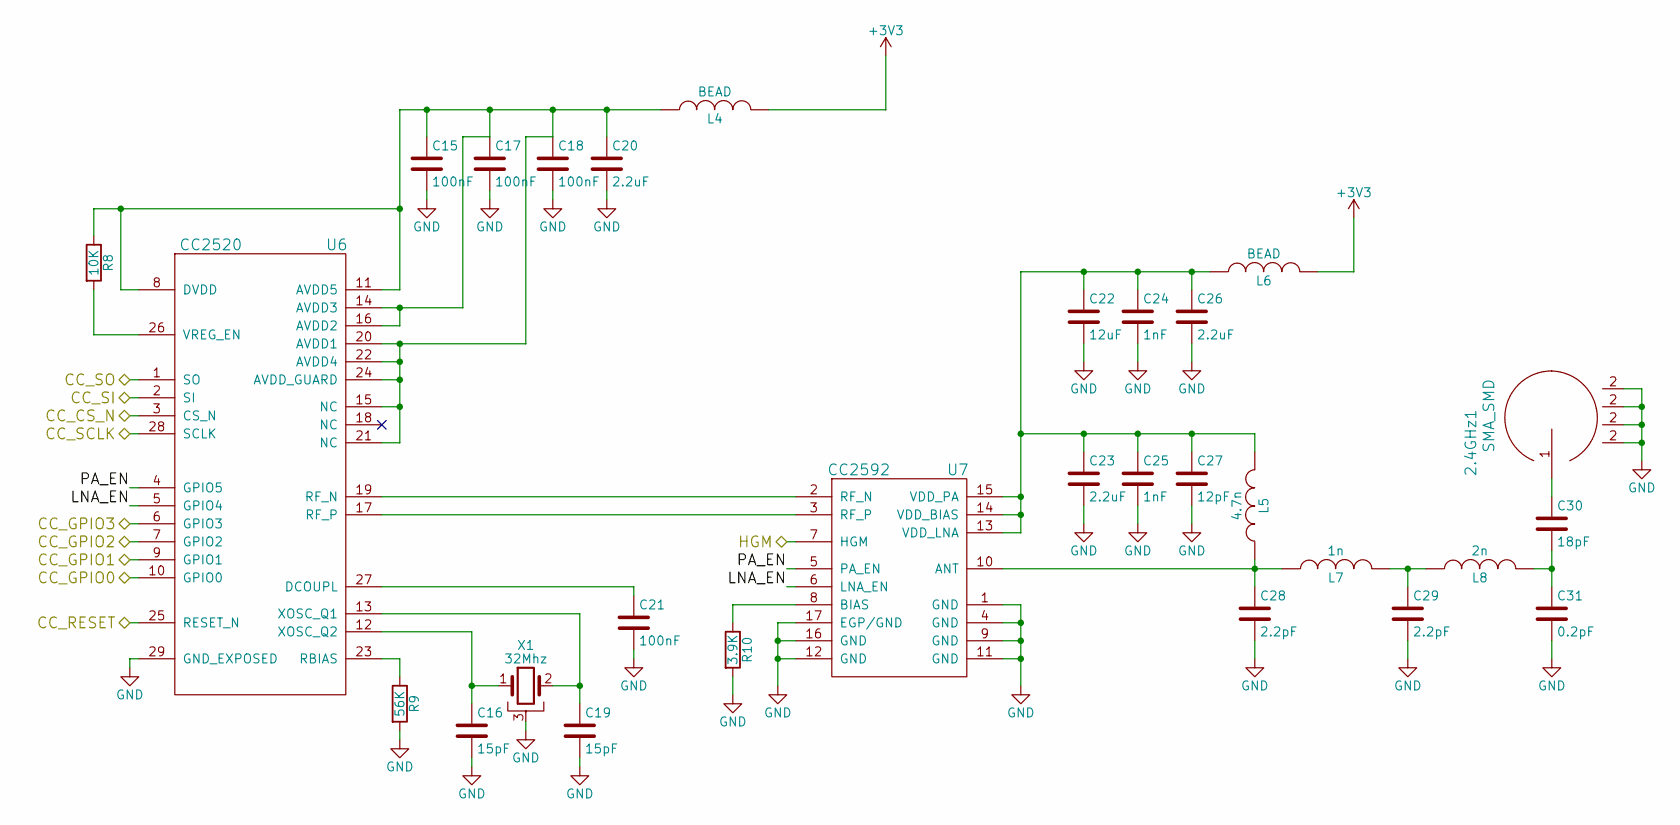
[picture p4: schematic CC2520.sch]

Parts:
2.4GHz1: SMA_SMD; SMA_THT_Jack_Straight
C15, C17, C18, C21: 100nF; C_0402
C16, C19: 15pF; C_0603
C20, C23, C26: 2.2uF; C_0603_1608Metric
C22: 12uF; C_1210_3225Metric
C24, C25: 1nF; C_0402
C27: 12pF; C_1210_3225Metric
C28, C29: 2.2pF; C_0603_1608Metric
C30: 18pF; C_0402
C31: 0.2pF; C_0402
L4, L6: BEAD; R_0603; MPN BLM18HE152SN1
L5: 4.7n; R_0402
L7: 1n; R_0402
L8: 2n; R_0402
R8: 10K; R_0402
R9: 56K; R_0402
R10: 3.9K; R_0402
U6: CC2520; QFN-28-1EP_5x5mm_Pitch0.5mm; MPN CC2520RHDR
U7: CC2592; QFN-16-1EP_4x4mm_Pitch0.65mm; MPN CC2592RGVR
X1: 32Mhz; Crystal_SMD_5032-4pin_5.0x3.2mm

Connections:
/CC2520/CC_CS_N: U6.3 (CS_N); also elsewhere on the board
/CC2520/CC_GPIO0: U6.10 (GPIO0); also elsewhere on the board
/CC2520/CC_GPIO1: U6.9 (GPIO1); also elsewhere on the board
/CC2520/CC_GPIO2: U6.7 (GPIO2); also elsewhere on the board
/CC2520/CC_GPIO3: U6.6 (GPIO3); also elsewhere on the board
/CC2520/CC_RESET: U6.25 (RESET_N); also elsewhere on the board
/CC2520/CC_SCLK: U6.28 (SCLK); also elsewhere on the board
/CC2520/CC_SI: U6.2 (SI); also elsewhere on the board
/CC2520/CC_SO: U6.1 (SO); also elsewhere on the board
/CC2520/HGM: U7.7 (HGM); also elsewhere on the board
/CC2520/LNA_EN: U6.5 (GPIO4), U7.6 (LNA_EN)
/CC2520/PA_EN: U6.4 (GPIO5), U7.5 (PA_EN)
GND: 2.4GHz1.2, C15.2, C16.2, C17.2, C18.2, C19.2, C20.2, C21.2, C22.2, C23.2, C24.2, C25.2, C26.2, C27.2, C28.2, C29.2, C31.2, R9.2, R10.2, U6.29 (GND_EXPOSED), U7.1 (GND), U7.4 (GND), U7.9 (GND), U7.11 (GND), U7.12 (GND), U7.16 (GND), U7.17 (EGP/GND), X1.3; also elsewhere on the board
unnamed: C15.1, C17.1, C18.1, C20.1, L4.1, R8.1, U6.8 (DVDD), U6.11 (AVDD5), U6.14 (AVDD3), U6.15 (NC), U6.16 (AVDD2), U6.20 (AVDD1), U6.21 (NC), U6.22 (AVDD4), U6.24 (AVDD_GUARD)
unnamed: C16.1, U6.12 (XOSC_Q2), X1.1
unnamed: C19.1, U6.13 (XOSC_Q1), X1.2
unnamed: C21.1, U6.27 (DCOUPL)
unnamed: C22.1, C23.1, C24.1, C25.1, C26.1, C27.1, L5.2, L6.1, U7.13 (VDD_LNA), U7.14 (VDD_BIAS), U7.15 (VDD_PA)
unnamed 216: C28.1, L5.1, L7.1, U7.10 (ANT); also elsewhere on the board
unnamed: C29.1, L7.2, L8.1
unnamed 218: 2.4GHz1.1, C30.1; also elsewhere on the board
unnamed: C30.2, C31.1, L8.2
unnamed: R8.2, U6.26 (VREG_EN)
unnamed: R9.1, U6.23 (RBIAS)
unnamed: R10.1, U7.8 (BIAS)
unnamed: U6.17 (RF_P), U7.3 (RF_P)
unnamed: U6.19 (RF_N), U7.2 (RF_N)

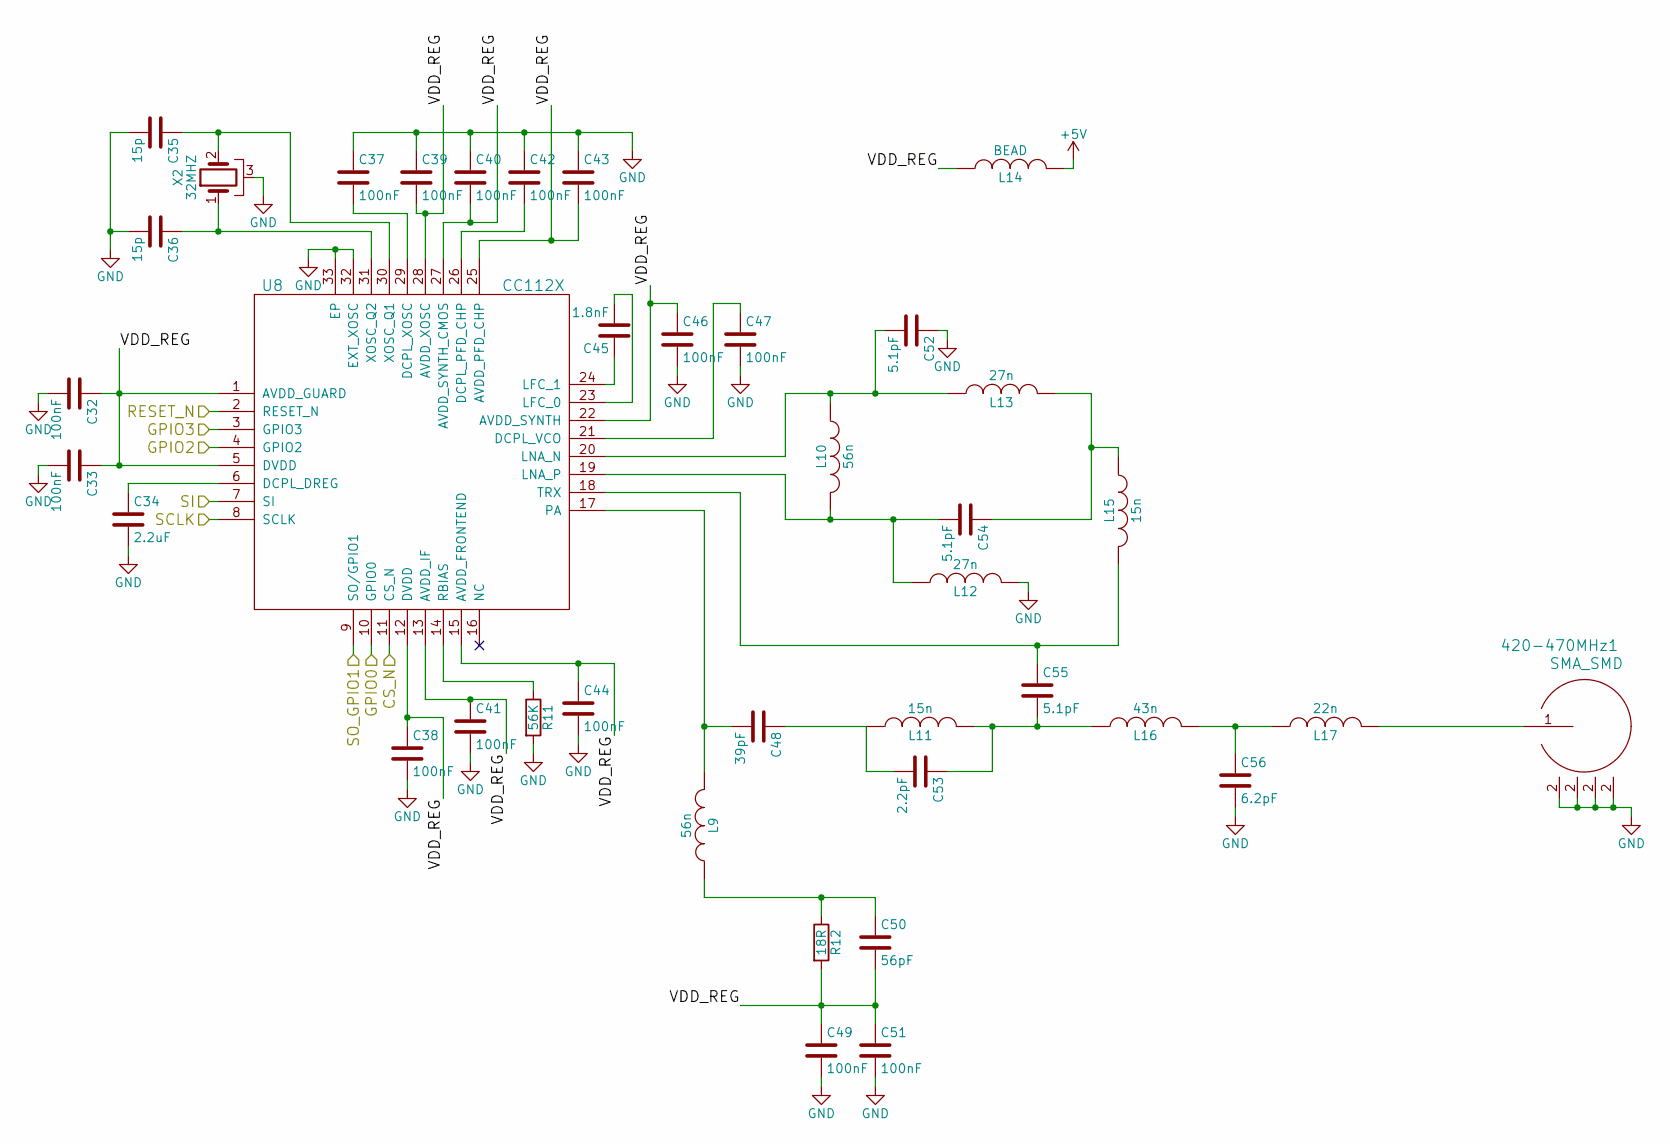
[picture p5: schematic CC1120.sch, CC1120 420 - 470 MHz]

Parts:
420-470MHz1: SMA_SMD; SMA_THT_Jack_Straight
C32, C33, C37, C38, C39, C40, C41, C42, C43, C44, C46, C47, C49, C51: 100nF; C_0402
C34: 2.2uF; C_0603
C35, C36: 15p; C_0603
C45: 1.8nF; C_0402
C48: 39pF; C_0402
C50: 56pF; C_0402
C52, C54, C55: 5.1pF; C_0402
C53: 2.2pF; C_0402
C56: 6.2pF; C_0402
L9, L10: 56n; R_0402
L11, L15: 15n; R_0402
L12, L13: 27n; R_0402
L14: BEAD; R_0603; MPN BLM18HE152SN1
L16: 43n; R_0402
L17: 22n; R_0402
R11: 56K; R_0402
R12: 18R; R_0402
U8: CC112X; QFN-32-1EP_5x5mm_Pitch0.5mm
X2: 32MHZ; Crystal_SMD_5032-4pin_5.0x3.2mm

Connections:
+5V: L14.2; also elsewhere on the board
/CC1120/CS_N: U8.11 (CS_N); also elsewhere on the board
/CC1120/GPIO0: U8.10 (GPIO0); also elsewhere on the board
/CC1120/GPIO2: U8.4 (GPIO2); also elsewhere on the board
/CC1120/GPIO3: U8.3 (GPIO3); also elsewhere on the board
/CC1120/SCLK: U8.8 (SCLK); also elsewhere on the board
/CC1120/SI: U8.7 (SI); also elsewhere on the board
/CC1120/SO_GPIO1: U8.9 (SO/GPIO1); also elsewhere on the board
/CC1120/VDD_REG: C32.1, C33.1, C38.1, C39.2, C40.2, C41.1, C43.2, C44.1, C46.1, C49.1, C50.2, C51.1, L14.1, R12.2, U8.1 (AVDD_GUARD), U8.5 (DVDD), U8.12 (DVDD), U8.13 (AVDD_IF), U8.15 (AVDD_FRONTEND), U8.22 (AVDD_SYNTH), U8.25 (AVDD_PFD_CHP), U8.27 (AVDD_SYNTH_CMOS), U8.28 (AVDD_XOSC)
/das_board/PA0: U8.2 (RESET_N); also elsewhere on the board
GND: 420-470MHz1.2, C32.2, C33.2, C34.2, C35.2, C36.2, C37.1, C38.2, C39.1, C40.1, C41.2, C42.1, C43.1, C44.2, C46.2, C47.2, C49.2, C51.2, C52.1, C56.2, L12.2, R11.2, U8.32 (EXT_XOSC), U8.33 (EP), X2.3; also elsewhere on the board
unnamed: C34.1, U8.6 (DCPL_DREG)
unnamed: C35.1, U8.30 (XOSC_Q1), X2.2
unnamed: C36.1, U8.31 (XOSC_Q2), X2.1
unnamed: C37.2, U8.29 (DCPL_XOSC)
unnamed: C42.2, U8.26 (DCPL_PFD_CHP)
unnamed: C45.1, U8.24 (LFC_1)
unnamed: C45.2, U8.23 (LFC_0)
unnamed: C47.1, U8.21 (DCPL_VCO)
unnamed: C48.1, C53.2, L11.1
unnamed 229: C48.2, L9.2, U8.17 (PA); also elsewhere on the board
unnamed: C50.1, L9.1, R12.1
unnamed: C52.2, L10.1, L13.1, U8.20 (LNA_N)
unnamed: C53.1, C55.2, L11.2, L16.1
unnamed: C54.1, L13.2, L15.1
unnamed: C54.2, L10.2, L12.1, U8.19 (LNA_P)
unnamed: C55.1, L15.2, U8.18 (TRX)
unnamed: C56.1, L16.2, L17.1
unnamed 273: 420-470MHz1.1, L17.2; also elsewhere on the board
unnamed: R11.1, U8.14 (RBIAS)

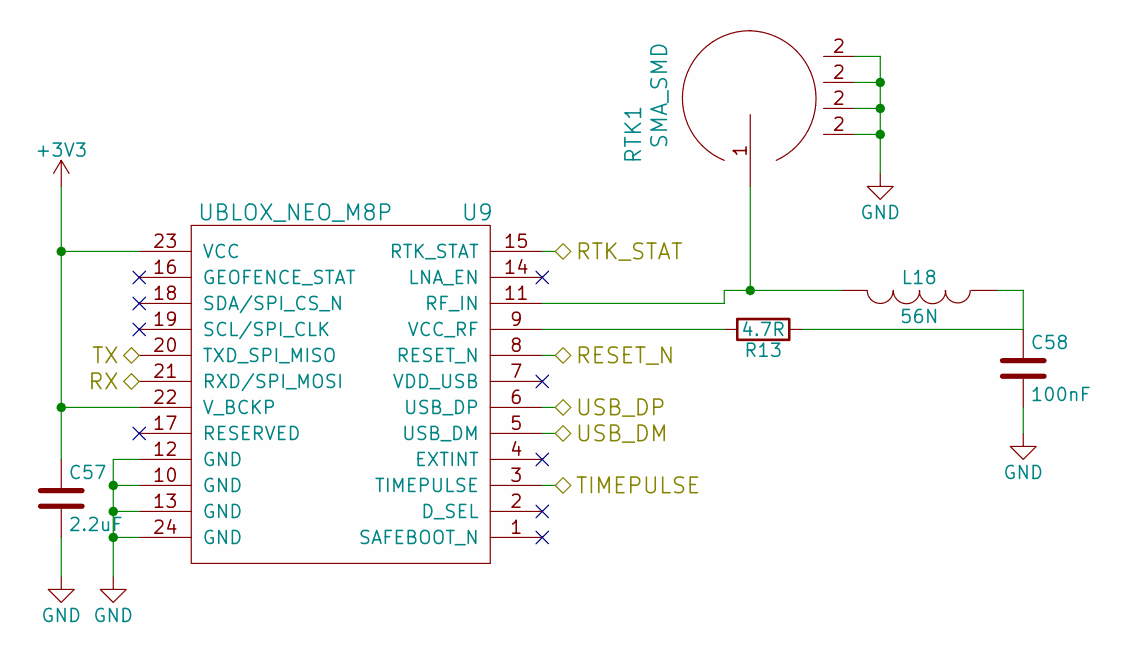
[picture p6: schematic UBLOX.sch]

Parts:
C57: 2.2uF; C_0603
C58: 100nF; C_0402
L18: 56N; R_0402
R13: 4.7R; R_0402
RTK1: SMA_SMD; SMA_THT_Jack_Straight
U9: UBLOX_NEO_M8P; U-BLOX-NEO-M8P

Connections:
GND: C57.2, C58.2, RTK1.2, U9.10 (GND), U9.12 (GND), U9.13 (GND), U9.24 (GND); also elsewhere on the board
unnamed: C58.1, L18.1, R13.1
unnamed 274: L18.2, RTK1.1, U9.11 (RF_IN); also elsewhere on the board
unnamed 283: R13.2, U9.9 (VCC_RF); also elsewhere on the board

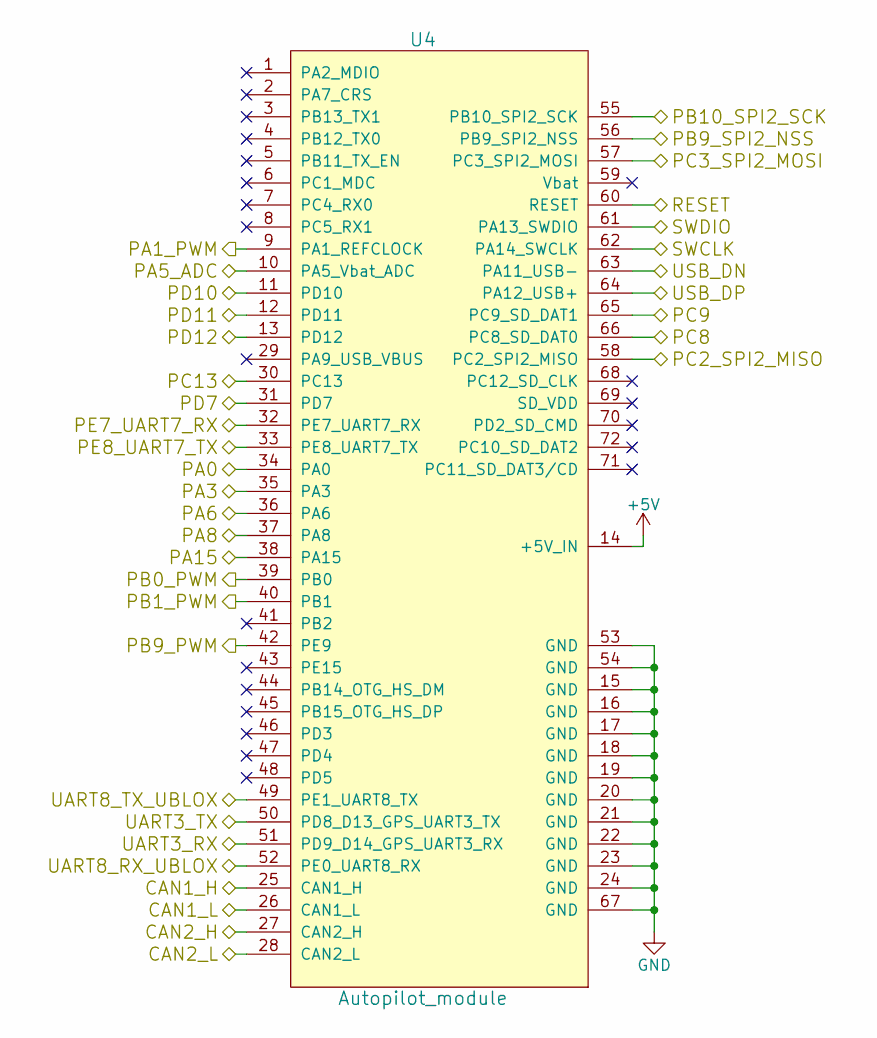
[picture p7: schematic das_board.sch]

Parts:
U4: Autopilot_module; Autopilot

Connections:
+5V: U4.14 (+5V_IN); also elsewhere on the board
/CC1120/GPIO0: U4.35 (PA3); also elsewhere on the board
/CC1120/GPIO2: U4.36 (PA6); also elsewhere on the board
/CC1120/GPIO3: U4.37 (PA8); also elsewhere on the board
/CC2520/CC_CS_N: U4.56 (PB9_SPI2_NSS); also elsewhere on the board
/CC2520/CC_GPIO0: U4.31 (PD7); also elsewhere on the board
/CC2520/CC_GPIO1: U4.13 (PD12); also elsewhere on the board
/CC2520/CC_GPIO2: U4.12 (PD11); also elsewhere on the board
/CC2520/CC_GPIO3: U4.11 (PD10); also elsewhere on the board
/CC2520/CC_RESET: U4.38 (PA15); also elsewhere on the board
/CC2520/CC_SCLK: U4.55 (PB10_SPI2_SCK); also elsewhere on the board
/CC2520/CC_SI: U4.57 (PC3_SPI2_MOSI); also elsewhere on the board
/CC2520/CC_SO: U4.58 (PC2_SPI2_MISO); also elsewhere on the board
/CC2520/HGM: U4.30 (PC13); also elsewhere on the board
/STM_RESET: U4.60 (RESET); also elsewhere on the board
/STM_SWCLK: U4.62 (PA14_SWCLK); also elsewhere on the board
/STM_SWDIO: U4.61 (PA13_SWDIO); also elsewhere on the board
/STM_USB_N: U4.63 (PA11_USB-); also elsewhere on the board
/STM_USB_P: U4.64 (PA12_USB+); also elsewhere on the board
/UART_RX_GPS_RASP: U4.51 (PD9_D14_GPS_UART3_RX); also elsewhere on the board
/UART_TX_GPS_RASP: U4.50 (PD8_D13_GPS_UART3_TX); also elsewhere on the board
/UBLOX/RX: U4.52 (PE0_UART8_RX); also elsewhere on the board
/UBLOX/TX: U4.49 (PE1_UART8_TX); also elsewhere on the board
/VBAT_ADC: U4.10 (PA5_Vbat_ADC); also elsewhere on the board
/das_board/CAN1_H: U4.25 (CAN1_H); also elsewhere on the board
/das_board/CAN1_L: U4.26 (CAN1_L); also elsewhere on the board
/das_board/CAN2_H: U4.27 (CAN2_H); also elsewhere on the board
/das_board/CAN2_L: U4.28 (CAN2_L); also elsewhere on the board
/das_board/PA0: U4.34 (PA0); also elsewhere on the board
/das_board/PA1_PWM: U4.9 (PA1_REFCLOCK); also elsewhere on the board
/das_board/PB0_PWM: U4.39 (PB0); also elsewhere on the board
/das_board/PB1_PWM: U4.40 (PB1); also elsewhere on the board
/das_board/PB9_PWM: U4.42 (PE9); also elsewhere on the board
/das_board/PC8: U4.66 (PC8_SD_DAT0); also elsewhere on the board
/das_board/PC9: U4.65 (PC9_SD_DAT1); also elsewhere on the board
/das_board/PE7_UART7_RX: U4.32 (PE7_UART7_RX); also elsewhere on the board
/das_board/PE8_UART7_TX: U4.33 (PE8_UART7_TX); also elsewhere on the board
GND: U4.15 (GND), U4.16 (GND), U4.17 (GND), U4.18 (GND), U4.19 (GND), U4.20 (GND), U4.21 (GND), U4.22 (GND), U4.23 (GND), U4.24 (GND), U4.53 (GND), U4.54 (GND), U4.67 (GND); also elsewhere on the board

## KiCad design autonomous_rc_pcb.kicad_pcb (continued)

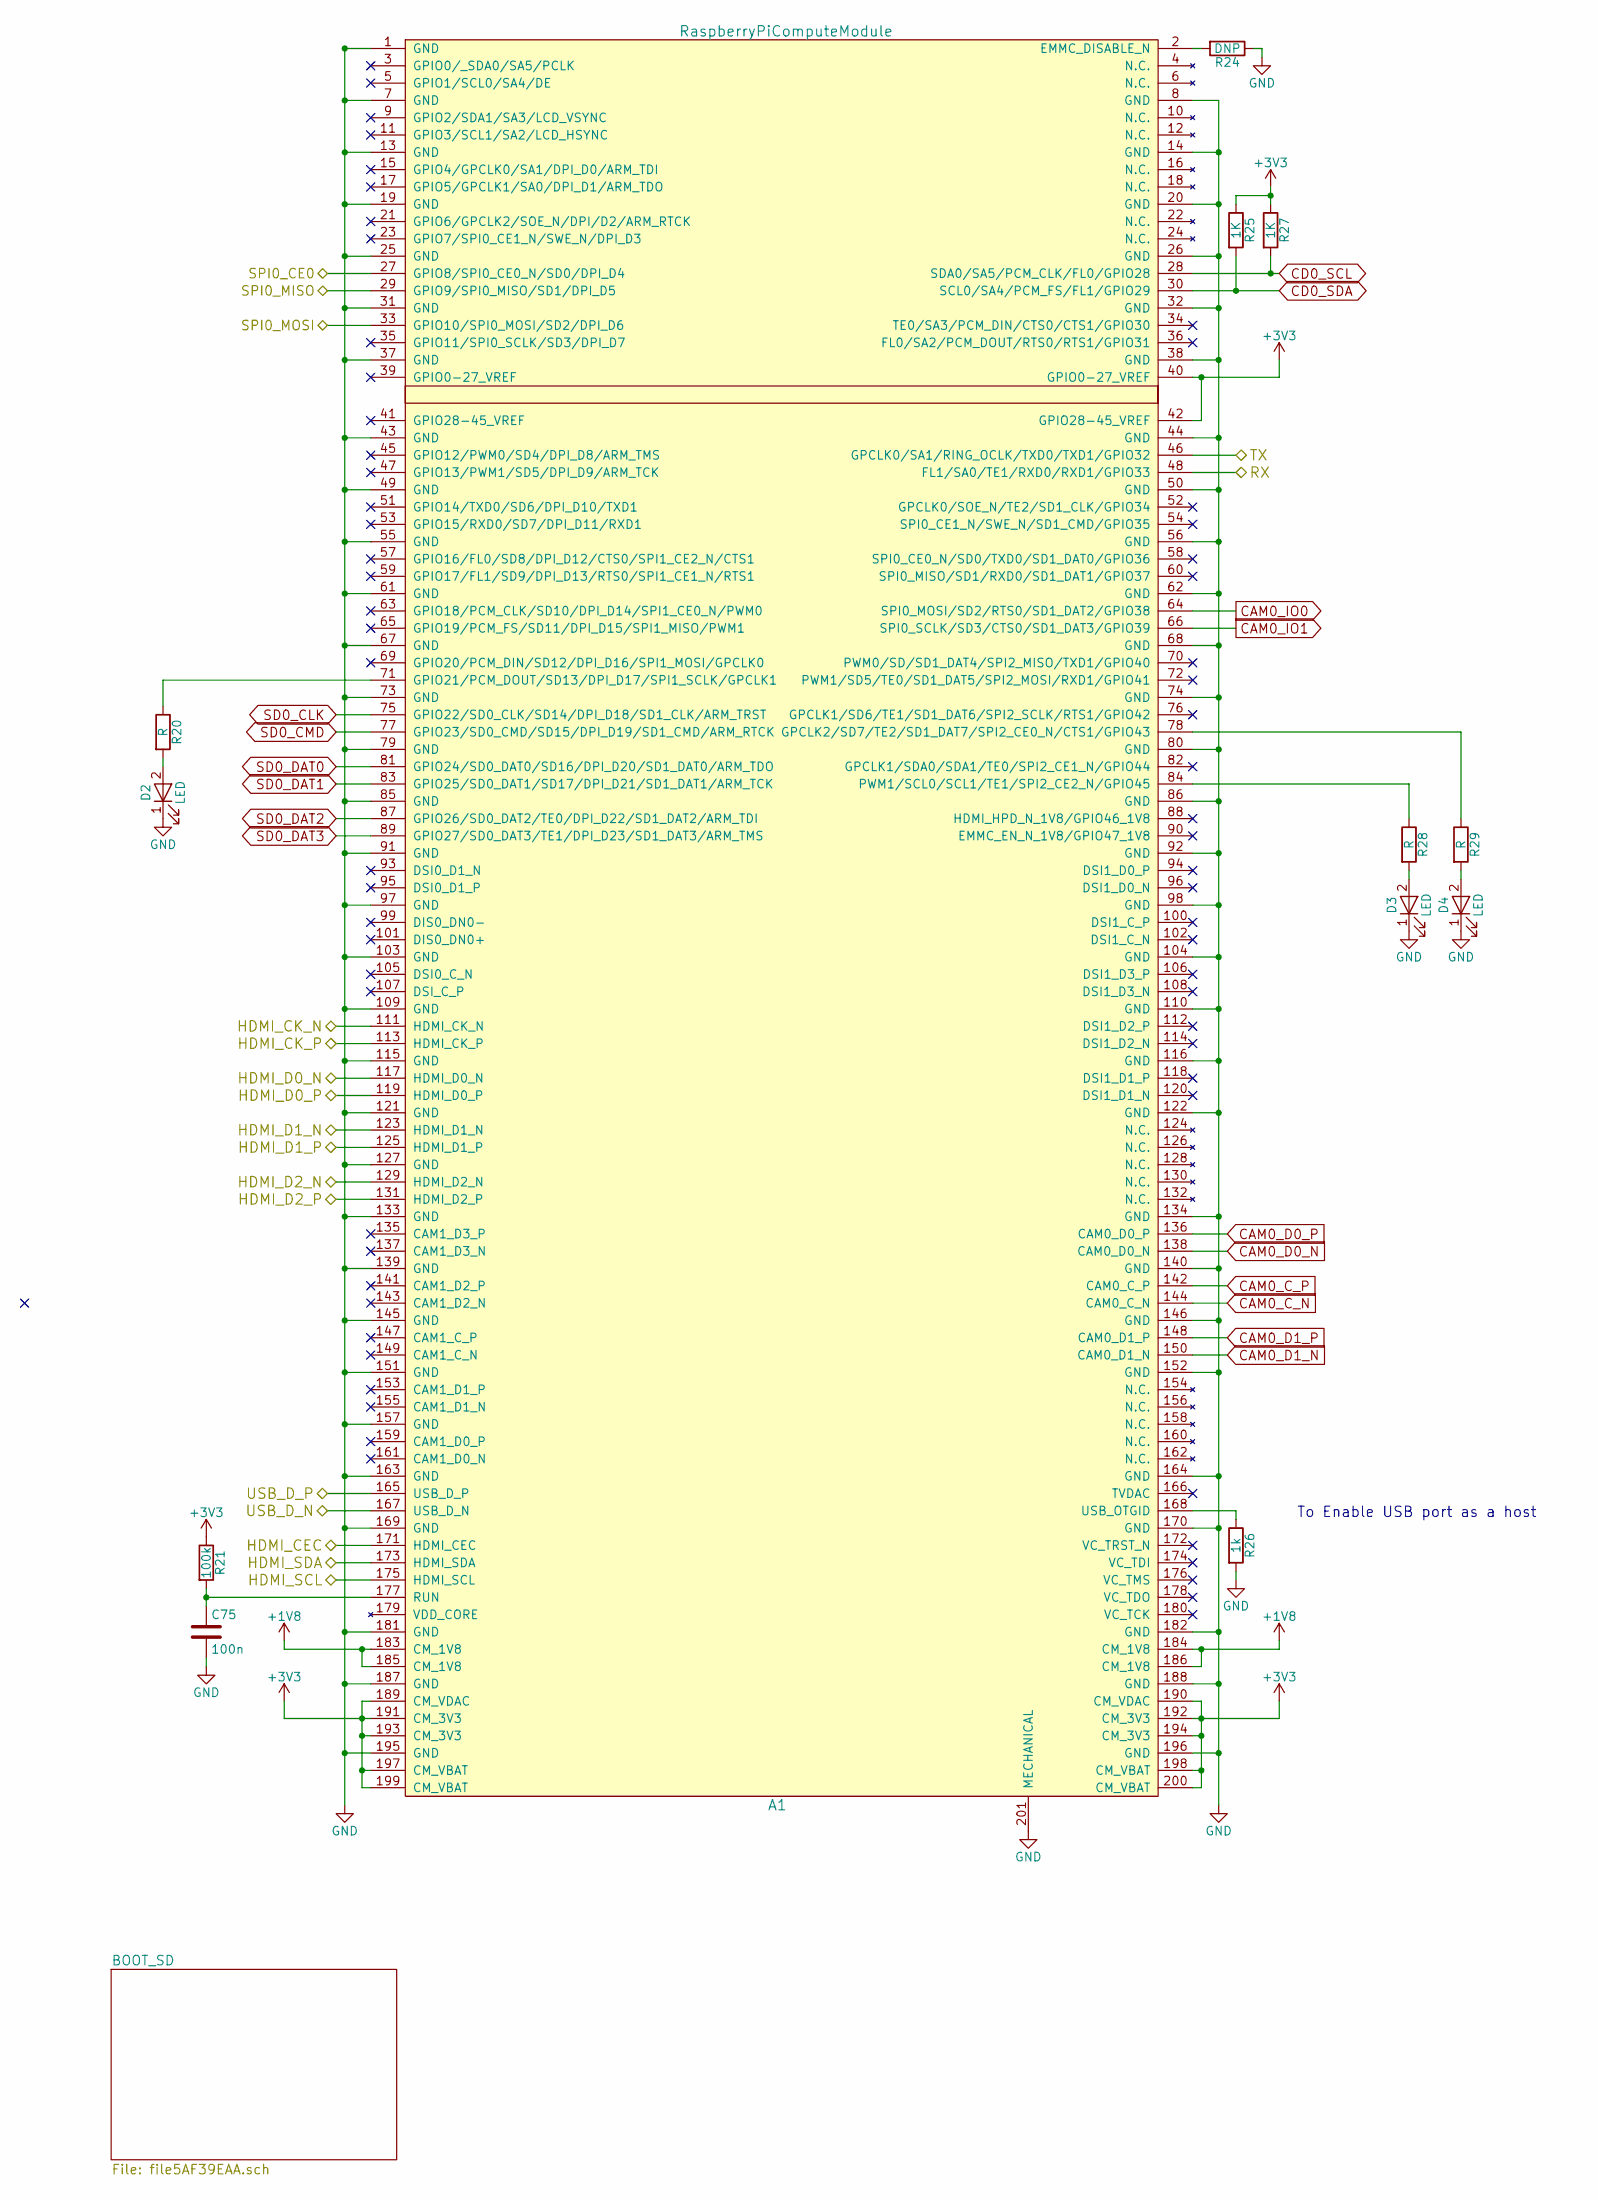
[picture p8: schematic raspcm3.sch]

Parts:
A1: RaspberryPiComputeModule; DDR2_TE_1473149-4
C75: 100n; C_0402
D2, D3, D4: LED; LED_0603
R20, R28, R29: R; R_0402
R21: 100k; R_0402
R24: DNP; R_0402
R25, R27: 1K; R_0402
R26: 1k; R_0402

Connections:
+1V8: A1.183 (CM_1V8), A1.184 (CM_1V8), A1.185 (CM_1V8), A1.186 (CM_1V8); also elsewhere on the board
/STM_RESET: A1.33 (GPIO10/SPI0_MOSI/SD2/DPI_D6); also elsewhere on the board
/STM_SWCLK: A1.27 (GPIO8/SPI0_CE0_N/SD0/DPI_D4); also elsewhere on the board
/STM_SWDIO: A1.29 (GPIO9/SPI0_MISO/SD1/DPI_D5); also elsewhere on the board
/UART_RX_GPS_RASP: A1.48 (FL1/SA0/TE1/RXD0/RXD1/GPIO33); also elsewhere on the board
/UART_TX_GPS_RASP: A1.46 (GPCLK0/SA1/RING_OCLK/TXD0/TXD1/GPIO32); also elsewhere on the board
/USB_HUB+: A1.165 (USB_D_P); also elsewhere on the board
/USB_HUB-: A1.167 (USB_D_N); also elsewhere on the board
/raspcm3/HDMI_CEC: A1.171 (HDMI_CEC); also elsewhere on the board
/raspcm3/HDMI_CK_N: A1.111 (HDMI_CK_N); also elsewhere on the board
/raspcm3/HDMI_CK_P: A1.113 (HDMI_CK_P); also elsewhere on the board
/raspcm3/HDMI_D0_N: A1.117 (HDMI_D0_N); also elsewhere on the board
/raspcm3/HDMI_D0_P: A1.119 (HDMI_D0_P); also elsewhere on the board
/raspcm3/HDMI_D1_N: A1.123 (HDMI_D1_N); also elsewhere on the board
/raspcm3/HDMI_D1_P: A1.125 (HDMI_D1_P); also elsewhere on the board
/raspcm3/HDMI_D2_N: A1.129 (HDMI_D2_N); also elsewhere on the board
/raspcm3/HDMI_D2_P: A1.131 (HDMI_D2_P); also elsewhere on the board
/raspcm3/HDMI_SCL: A1.175 (HDMI_SCL); also elsewhere on the board
/raspcm3/HDMI_SDA: A1.173 (HDMI_SDA); also elsewhere on the board
CAM0_C_N: A1.144 (CAM0_C_N); also elsewhere on the board
CAM0_C_P: A1.142 (CAM0_C_P); also elsewhere on the board
CAM0_D0_N: A1.138 (CAM0_D0_N); also elsewhere on the board
CAM0_D0_P: A1.136 (CAM0_D0_P); also elsewhere on the board
CAM0_D1_N: A1.150 (CAM0_D1_N); also elsewhere on the board
CAM0_D1_P: A1.148 (CAM0_D1_P); also elsewhere on the board
CAM0_IO0: A1.64 (SPI0_MOSI/SD2/RTS0/SD1_DAT2/GPIO38); also elsewhere on the board
CAM0_IO1: A1.66 (SPI0_SCLK/SD3/CTS0/SD1_DAT3/GPIO39); also elsewhere on the board
CD0_SCL: A1.28 (SDA0/SA5/PCM_CLK/FL0/GPIO28), R27.2; also elsewhere on the board
CD0_SDA: A1.30 (SCL0/SA4/PCM_FS/FL1/GPIO29), R25.2; also elsewhere on the board
GND: A1.1 (GND), A1.7 (GND), A1.8 (GND), A1.13 (GND), A1.14 (GND), A1.19 (GND), A1.20 (GND), A1.25 (GND), A1.26 (GND), A1.31 (GND), A1.32 (GND), A1.37 (GND), A1.38 (GND), A1.43 (GND), A1.44 (GND), A1.49 (GND), A1.50 (GND), A1.55 (GND), A1.56 (GND), A1.61 (GND), A1.62 (GND), A1.67 (GND), A1.68 (GND), A1.73 (GND), A1.74 (GND), A1.79 (GND), A1.80 (GND), A1.85 (GND), A1.86 (GND), A1.91 (GND), A1.92 (GND), A1.97 (GND), A1.98 (GND), A1.103 (GND), A1.104 (GND), A1.109 (GND), A1.110 (GND), A1.115 (GND), A1.116 (GND), A1.121 (GND), A1.122 (GND), A1.127 (GND), A1.133 (GND), A1.134 (GND), A1.139 (GND), A1.140 (GND), A1.145 (GND), A1.146 (GND), A1.151 (GND), A1.152 (GND), A1.157 (GND), A1.163 (GND), A1.164 (GND), A1.169 (GND), A1.170 (GND), A1.181 (GND), A1.182 (GND), A1.187 (GND), A1.188 (GND), A1.195 (GND), A1.196 (GND), A1.201 (MECHANICAL), C75.2, D2.1 (K), D3.1 (K), D4.1 (K), R24.1, R26.2; also elsewhere on the board
unnamed: A1.2 (EMMC_DISABLE_N), R24.2
unnamed: A1.71 (GPIO21/PCM_DOUT/SD13/DPI_D17/SPI1_SCLK/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), R20.1
unnamed: A1.78 (GPCLK2/SD7/TE2/SD1_DAT7/SPI2_CE0_N/CTS1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), R29.1
unnamed: A1.84 (PWM1/SCL0/SCL1/TE1/SPI2_CE2_N/GPIO45), R28.1
unnamed: A1.168 (USB_OTGID), R26.1
unnamed: A1.177 (RUN), C75.1, R21.2
unnamed: D2.2 (A), R20.2
unnamed: D3.2 (A), R28.2
unnamed: D4.2 (A), R29.2
SD0_CLK: A1.75 (GPIO22/SD0_CLK/SD14/DPI_D18/SD1_CLK/ARM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); also elsewhere on the board
SD0_CMD: A1.77 (GPIO23/SD0_CMD/SD15/DPI_D19/SD1_CMD/ARM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); also elsewhere on the board
SD0_DAT0: A1.81 (GPIO24/SD0_DAT0/SD16/DPI_D20/SD1_DAT0/A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); also elsewhere on the board
SD0_DAT1: A1.83 (GPIO25/SD0_DAT1/SD17/DPI_D21/SD1_DAT1/A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); also elsewhere on the board
SD0_DAT2: A1.87 (GPIO26/SD0_DAT2/TE0/DPI_D22/SD1_DAT2/AR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); also elsewhere on the board
SD0_DAT3: A1.89 (GPIO27/SD0_DAT3/TE1/DPI_D23/SD1_DAT3/AR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); also elsewhere on the board

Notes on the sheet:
To Enable USB port as a host

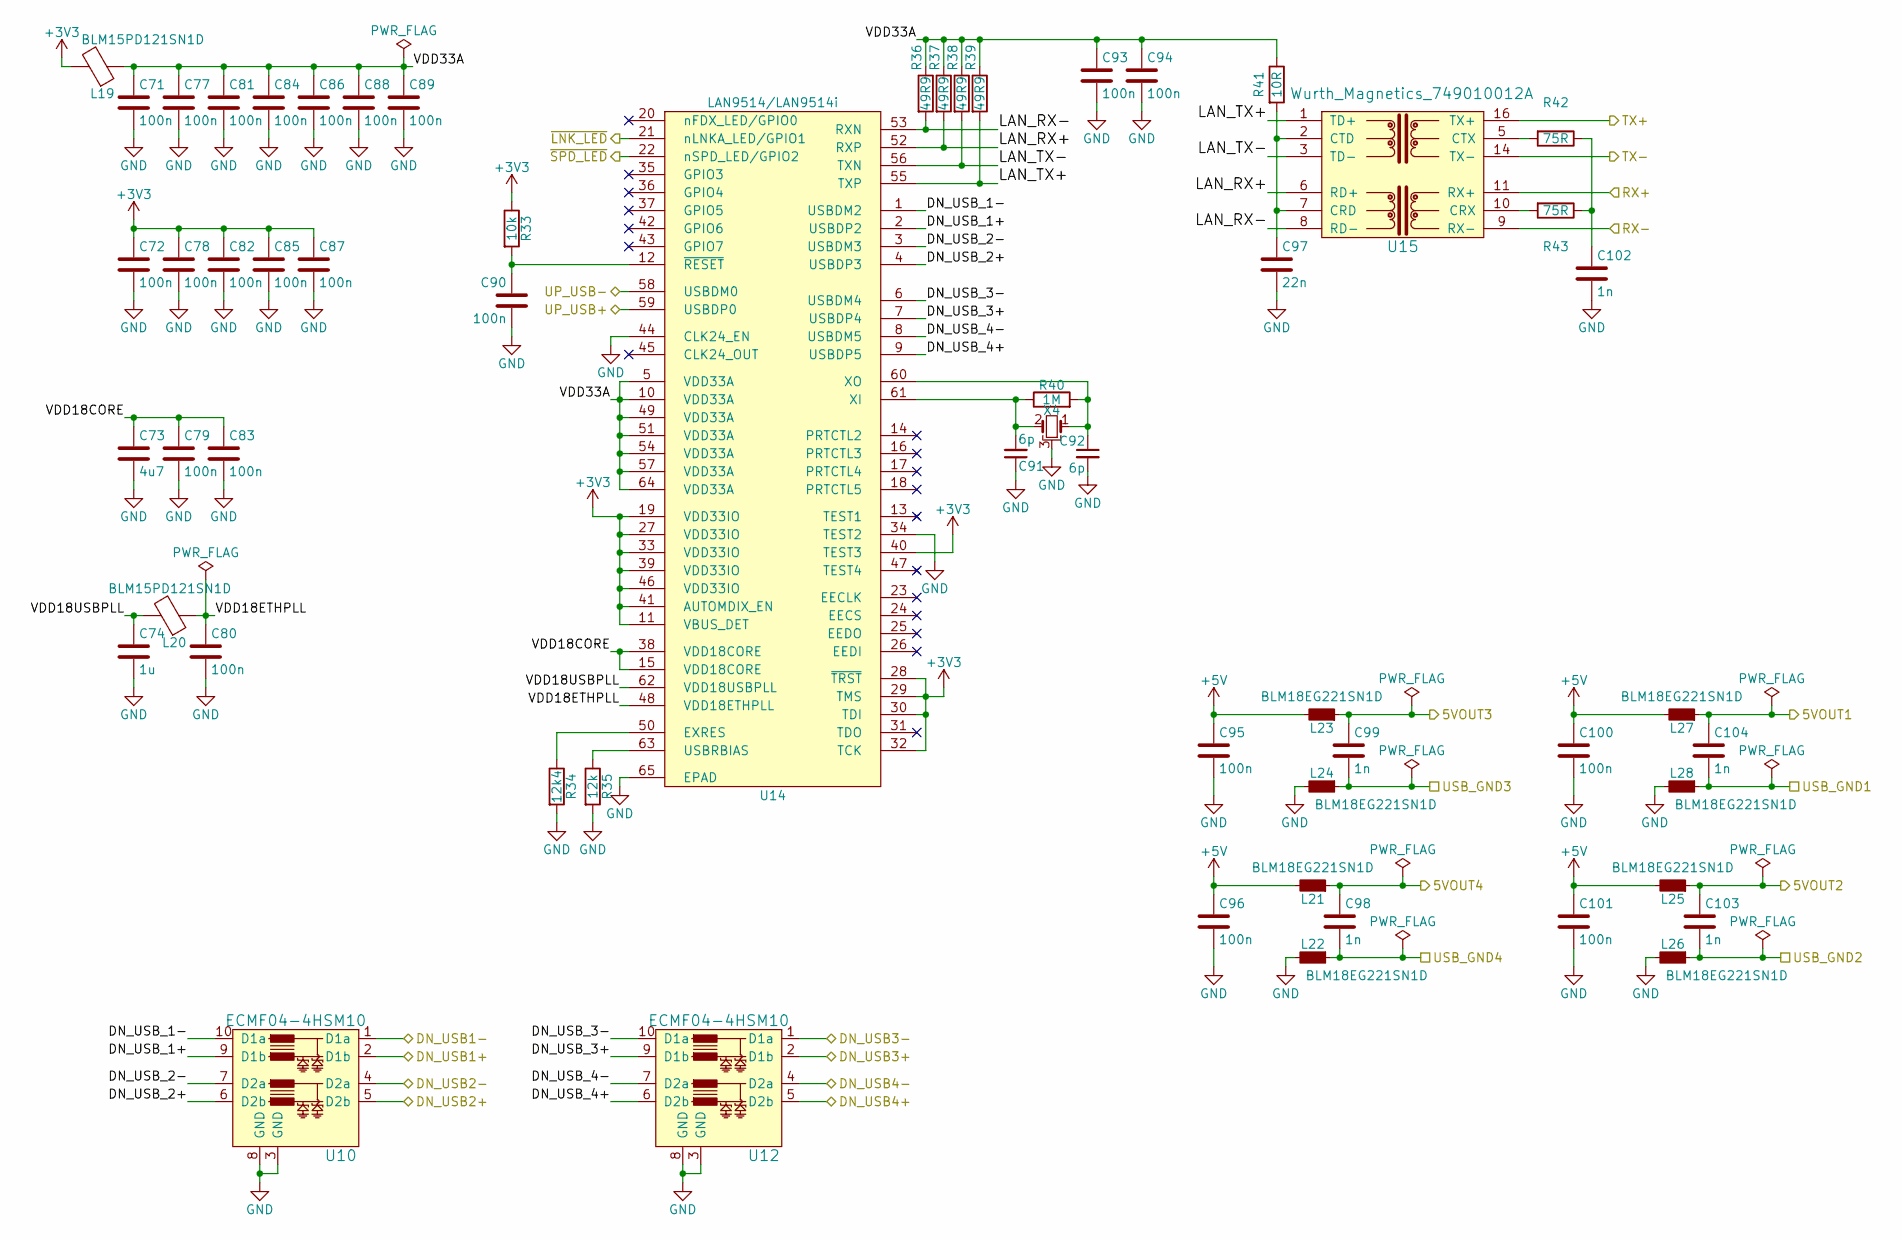
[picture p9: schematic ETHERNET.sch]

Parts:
C71, C72, C77, C78, C79, C80, C81, C82, C83, C84, C85, C86, C87, C88, C89, C90, C93, C94, C95, C96, C100, C101: 100n; C_0402
C73: 4u7; C_0603
C74: 1u; C_0402
C91, C92: 6p; C_0402
C97: 22n; C_0805
C98, C99, C103, C104: 1n; C_0402
C102: 1n; C_0805
L19, L20: BLM15PD121SN1D; R_0402
L21, L22, L23, L24, L25, L26, L27, L28: BLM18EG221SN1D; R_0603; MPN BLM18EG221SN1D
R33: 10k; R_0402
R34: 12k4; R_0402
R35: 12k; R_0402
R36, R37, R38, R39: 49R9; R_0402
R40: 1M; R_0402
R41: 10R; R_0402
R42, R43: 75R; R_0402
U10, U12: ECMF04-4HSM10; UDFN-10_1.35x2.6mm_Pitch0.5mm; MPN ECMF04-4HSM10
U14: LAN9514/LAN9514i; QFN-64-1EP_9x9mm_Pitch0.5mm; MPN LAN9514-JZX
U15: Wurth_Magnetics_749010012A; Wurth_749010012A; MPN 749010012A
X4: XRCGB25M000F2P00R0; XRCGB

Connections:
+5V: C95.1, C96.1, C100.1, C101.1, L21.2, L23.2, L25.2, L27.2; also elsewhere on the board
/ETHERNET/5VOUT1: C104.1, L27.1; also elsewhere on the board
/ETHERNET/5VOUT2: C103.1, L25.1; also elsewhere on the board
/ETHERNET/5VOUT3: C99.1, L23.1; also elsewhere on the board
/ETHERNET/5VOUT4: C98.1, L21.1; also elsewhere on the board
/ETHERNET/DN_USB1+: U10.2 (D1b); also elsewhere on the board
/ETHERNET/DN_USB1-: U10.1 (D1a); also elsewhere on the board
/ETHERNET/DN_USB2+: U10.5 (D2b); also elsewhere on the board
/ETHERNET/DN_USB2-: U10.4 (D2a); also elsewhere on the board
/ETHERNET/DN_USB3+: U12.2 (D1b); also elsewhere on the board
/ETHERNET/DN_USB3-: U12.1 (D1a); also elsewhere on the board
/ETHERNET/DN_USB4+: U12.5 (D2b); also elsewhere on the board
/ETHERNET/DN_USB4-: U12.4 (D2a); also elsewhere on the board
/ETHERNET/DN_USB_1+: U10.9 (D1b), U14.2 (USBDP2)
/ETHERNET/DN_USB_1-: U10.10 (D1a), U14.1 (USBDM2)
/ETHERNET/DN_USB_2+: U10.6 (D2b), U14.4 (USBDP3)
/ETHERNET/DN_USB_2-: U10.7 (D2a), U14.3 (USBDM3)
/ETHERNET/DN_USB_3+: U12.9 (D1b), U14.7 (USBDP4)
/ETHERNET/DN_USB_3-: U12.10 (D1a), U14.6 (USBDM4)
/ETHERNET/DN_USB_4+: U12.6 (D2b), U14.9 (USBDP5)
/ETHERNET/DN_USB_4-: U12.7 (D2a), U14.8 (USBDM5)
/ETHERNET/LAN_RX+: R37.2, U14.52 (RXP), U15.6 (RD+)
/ETHERNET/LAN_RX-: R36.2, U14.53 (RXN), U15.8 (RD-)
/ETHERNET/LAN_TX+: R39.2, U14.55 (TXP), U15.1 (TD+)
/ETHERNET/LAN_TX-: R38.2, U14.56 (TXN), U15.3 (TD-)
/ETHERNET/RX+: U15.11 (RX+); also elsewhere on the board
/ETHERNET/RX-: U15.9 (RX-); also elsewhere on the board
/ETHERNET/TX+: U15.16 (TX+); also elsewhere on the board
/ETHERNET/TX-: U15.14 (TX-); also elsewhere on the board
/ETHERNET/USB_GND1: C104.2, L28.1; also elsewhere on the board
/ETHERNET/USB_GND2: C103.2, L26.1; also elsewhere on the board
/ETHERNET/USB_GND3: C99.2, L24.1; also elsewhere on the board
/ETHERNET/USB_GND4: C98.2, L22.1; also elsewhere on the board
/ETHERNET/VDD18CORE: C73.1, C79.1, C83.1, U14.15 (VDD18CORE), U14.38 (VDD18CORE)
/ETHERNET/VDD18ETHPLL: C80.1, L20.1, U14.48 (VDD18ETHPLL)
/ETHERNET/VDD18USBPLL: C74.1, L20.2, U14.62 (VDD18USBPLL)
/ETHERNET/VDD33A: C71.1, C77.1, C81.1, C84.1, C86.1, C88.1, C89.1, C93.1, C94.1, L19.1, R36.1, R37.1, R38.1, R39.1, R41.1, U14.5 (VDD33A), U14.10 (VDD33A), U14.49 (VDD33A), U14.51 (VDD33A), U14.54 (VDD33A), U14.57 (VDD33A), U14.64 (VDD33A)
/ETHERNET/~LNK_LED: U14.21 (nLNKA_LED/GPIO1); also elsewhere on the board
/ETHERNET/~SPD_LED: U14.22 (nSPD_LED/GPIO2); also elsewhere on the board
/USB_ETHER+: U14.59 (USBDP0); also elsewhere on the board
/USB_ETHER-: U14.58 (USBDM0); also elsewhere on the board
GND: C71.2, C72.2, C73.2, C74.2, C77.2, C78.2, C79.2, C80.2, C81.2, C82.2, C83.2, C84.2, C85.2, C86.2, C87.2, C88.2, C89.2, C90.2, C91.1, C92.2, C93.2, C94.2, C95.2, C96.2, C97.2, C100.2, C101.2, C102.2, L22.2, L24.2, L26.2, L28.2, R34.2, R35.2, U10.3 (GND), U10.8 (GND), U12.3 (GND), U12.8 (GND), U14.34 (TEST2), U14.44 (CLK24_EN), U14.65 (EPAD), X4.3; also elsewhere on the board
unnamed: C90.1, R33.2, U14.12 (~RESET)
unnamed: C91.2, R40.1, U14.61 (XI), X4.2
unnamed: C92.1, R40.2, U14.60 (XO), X4.1
unnamed: C97.1, R41.2, U15.2 (CTD), U15.7 (CRD)
unnamed: C102.1, R42.1, R43.1
unnamed: R34.1, U14.50 (EXRES)
unnamed: R35.1, U14.63 (USBRBIAS)
unnamed: R42.2, U15.5 (CTX)
unnamed: R43.2, U15.10 (CRX)

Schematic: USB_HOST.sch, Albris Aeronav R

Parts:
C59, C60, C61, C62, C63, C65, C66, C69, C70: 100n; C_0402
C64: 9p; C_0603_1608Metric; MPN GRM1555C1H9R0CA01D
C67: 9p; C_0603_1608Metric
C68: 4u7 10V; C_0603
R14, R16, R17, R18, R19: 100k; R_0402
R15: 12k0; R_0402
U13: USB2514Bi; QFN36_5m5X5m5; MPN USB2514B/M2
X3: XRCGB24M000F2P00R0; XRCGB

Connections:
/STM_USB_N: U13.1 (USBDM_DN1/PRT_DIS_M1); also elsewhere on the board
/STM_USB_P: U13.2 (USBDP_DN1/PRT_DIS_P1); also elsewhere on the board
/UBLOX_USB+: U13.4 (USBDP_DN2/PRT_DIS_P2); also elsewhere on the board
/UBLOX_USB-: U13.3 (USBDM_DN2/PRT_DIS_M2); also elsewhere on the board
/USB_ETHER+: U13.7 (USBDP_DN3/PRT_DIS_P3); also elsewhere on the board
/USB_ETHER-: U13.6 (USBDM_DN3/PRT_DIS_M3); also elsewhere on the board
/USB_HUB+: U13.31 (USBUP_DP); also elsewhere on the board
/USB_HUB-: U13.30 (USBUP_DM); also elsewhere on the board
GND: C59.2, C60.2, C61.2, C62.2, C63.2, C64.1, C65.2, C66.2, C67.1, C68.2, C69.2, C70.2, R15.1, R16.2, R17.2, R18.2, R19.2, U13.37 (VSS(PAD)), X3.3; also elsewhere on the board
unnamed: C64.2, U13.33 (XTALIN/CLKIN), X3.1
unnamed: C66.1, R14.1, U13.26 (RESET_N)
unnamed: C67.2, U13.32 (XTALOUT), X3.2
unnamed: C69.1, U13.34 (PLLFILT)
unnamed: C70.1, U13.14 (CRFILT)
unnamed: R15.2, U13.35 (RBIAS)
unnamed: R16.1, U13.22 (SDA/SMBDATA/NON_REM1)
unnamed: R17.1, U13.28 (SUSP_IND/LOCAL_PWR/NON_REM0)
unnamed: R18.1, U13.25 (HS_IND/CFG_SEL1)
unnamed: R19.1, U13.24 (SCL/SMBCLK/CFG_SEL0)

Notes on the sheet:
pin 15

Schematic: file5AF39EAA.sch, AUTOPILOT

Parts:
C76: 100n; C_0402
J9: Micro_SD_Card; microSD_Card_Receptacle_Wurth_693072010801
U11: CM1624; UDFN-16-1EP_3.3x1.35mm_Pitch0.4mm

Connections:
GND: C76.2, J9.6 (VSS), J9.9 (SHIELD), U11.17 (GND); also elsewhere on the board
unnamed: C76.1, J9.4 (VDD), U11.4 (SDESD1)
unnamed: J9.1 (DAT2), U11.8 (SDData2)
unnamed: J9.2 (DAT3/CD), U11.7 (SDData3)
unnamed: J9.3 (CMD), U11.6 (SDCMD)
unnamed: J9.5 (CLK), U11.3 (SDCLK)
unnamed: J9.7 (DAT0), U11.2 (SDData0)
unnamed: J9.8 (DAT1), U11.1 (SDData1)
SD0_CLK: U11.14 (CLK); also elsewhere on the board
SD0_CMD: U11.11 (CMD); also elsewhere on the board
SD0_DAT0: U11.15 (DATA0); also elsewhere on the board
SD0_DAT1: U11.16 (DATA1); also elsewhere on the board
SD0_DAT2: U11.9 (Data2); also elsewhere on the board
SD0_DAT3: U11.10 (Data3); also elsewhere on the board

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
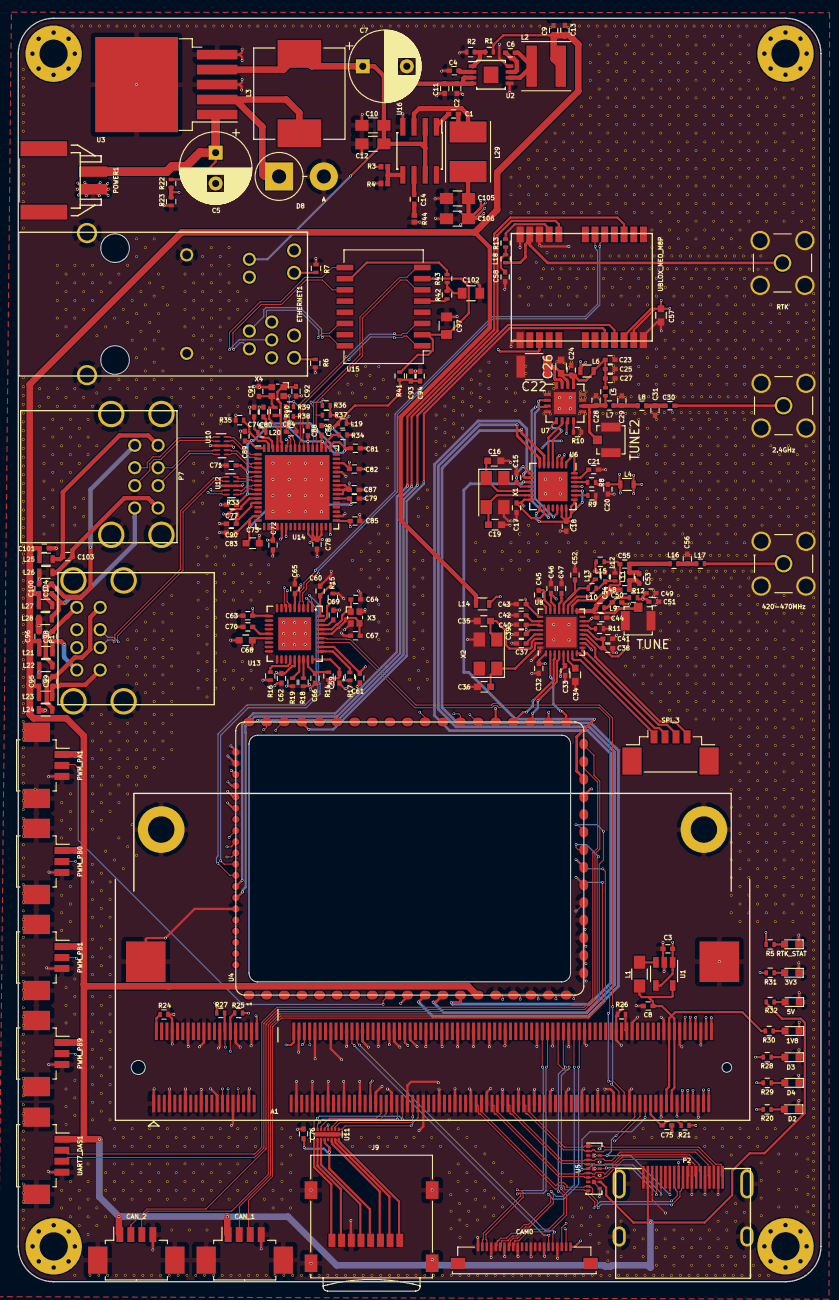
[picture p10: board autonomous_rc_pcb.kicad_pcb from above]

Board: 6 copper layers, 91.1 x 143.4 mm, 228 parts (0 on the bottom side), 209 nets.

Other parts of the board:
2.4GHz, 420-470MHz: SMA_SMD; SMA_THT_Jack_Straight
5V: 5V; LED_0603
P7: USB_A_Vertical; USB_A_Stacked
RTK: SMA_SMD; SMA_THT_Jack_Straight
RTK_STAT: RTK_STAT; LED_0603
TUNE, TUNE2: U.FL-R-SMT
UBLOX_NEO_M8P: UBLOX_NEO_M8P; U-BLOX-NEO-M8P

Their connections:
/ETHERNET/5VOUT1: P7.1; also elsewhere on the board
/ETHERNET/5VOUT2: P7.6; also elsewhere on the board
/ETHERNET/DN_USB1+: P7.3; also elsewhere on the board
/ETHERNET/DN_USB1-: P7.2; also elsewhere on the board
/ETHERNET/DN_USB2+: P7.8; also elsewhere on the board
/ETHERNET/DN_USB2-: P7.7; also elsewhere on the board
/ETHERNET/USB_GND1: P7.4; also elsewhere on the board
/ETHERNET/USB_GND2: P7.9; also elsewhere on the board
/UBLOX/RTK_STAT: UBLOX_NEO_M8P.15; also elsewhere on the board
/UBLOX/RX: UBLOX_NEO_M8P.21; also elsewhere on the board
/UBLOX/TX: UBLOX_NEO_M8P.20; also elsewhere on the board
/UBLOX_USB+: UBLOX_NEO_M8P.6; also elsewhere on the board
/UBLOX_USB-: UBLOX_NEO_M8P.5; also elsewhere on the board
/das_board/PC8: UBLOX_NEO_M8P.8; also elsewhere on the board
/das_board/PC9: UBLOX_NEO_M8P.3; also elsewhere on the board
GND: 2.4GHz.2, 5V.1, 420-470MHz.2, P7.5, RTK.2, RTK_STAT.1, TUNE.2, TUNE2.2, UBLOX_NEO_M8P.10, UBLOX_NEO_M8P.12, UBLOX_NEO_M8P.13, UBLOX_NEO_M8P.24; also elsewhere on the board
unnamed 216: TUNE2.1; also elsewhere on the board
unnamed 218: 2.4GHz.1; also elsewhere on the board
unnamed 229: TUNE.1; also elsewhere on the board
unnamed 253: RTK_STAT.2; also elsewhere on the board
unnamed 259: 5V.2; also elsewhere on the board
unnamed 273: 420-470MHz.1; also elsewhere on the board
unnamed 274: RTK.1, UBLOX_NEO_M8P.11; also elsewhere on the board
unnamed 283: UBLOX_NEO_M8P.9; also elsewhere on the board

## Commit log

2018-05-23 beta
    beta pcb version 0.001V
    [CC1120.sch, CC2520.sch, ETHERNET.sch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]
2018-05-24 added rf stitching, connector names
    [autonomous_rc_pcb.kicad_pcb]
2018-05-24 less stiching, added 3d models
    [autonomous_rc_pcb.kicad_pcb]
2018-05-24 added bom
    [bom_kicost.xlsx]
2018-05-25 tuned rf
    added u.fl connectors to tune line
    moved some lines under rf components
    [CC1120.sch, CC2520.sch, ETHERNET.sch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]
2018-05-29 stitched pcb, tuned rf
    [autonomous_rc_pcb.kicad_pcb]
